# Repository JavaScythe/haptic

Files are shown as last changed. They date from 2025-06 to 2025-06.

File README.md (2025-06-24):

# haptic
8 channel 2A motor with flyback protection USB controller with 5 extra exposed GPIOs

Why? To take advantage of the low pricing of these motors, while driving them in a cost efficient but low latency and sufficiently powered manner.





### BOM
|Name |Quantity|Price Total  |Link  |
|---|---|---|---|
|RK-370|8|24.37|aliexpress.us/item/3256806031375057.html|
|PCBA|2 (minimum)|25.09|JLCPCB, see gerbers|

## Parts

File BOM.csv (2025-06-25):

Name | Quantity | Price | Total | Link
RK-370 | 8 | 24.37 | aliexpress.us/item/3256806031375057.html
PCBA | 2 | 25.09 | JLCPCB see gerbers

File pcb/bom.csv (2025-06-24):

Designator | Footprint | Quantity | Value | LCSC Part #
C1, C2 | 0603 | 2 | 10uF
C3 | 0603 | 1 | 100nF
C4 | 0603 | 1 | 1nF
D1, D3, D4, D5, D6, D7, D8, D9 | D_SOD-123 | 8 | D
D2 | 0603 | 1 | 0603
J1 | PinHeader_1x05_P2.54mm_Vertical | 1 | SWD
J2 | CONN-TH_DB301V-3.5-2P-GN | 1 | Vin
J3 | CONN-TH_DB301V-3.5-2P-GN | 1 | Common High
J4 | PinHeader_1x03_P2.54mm_Vertical | 1 | Extra
J5, J6, J7, J8 | CONN-TH_DB301V-3.5-2P-GN | 4 | Motor
Q1, Q2, Q3, Q4, Q5, Q6, Q7, Q8 | SOT-23 | 8 | AO3400A
R1, R2 | 0603 | 2 | C107701
R10, R12, R13, R14, R15, R6, R8 | 0603 | 7 | 100
R11, R16, R17, R18, R19, R7, R9 | 0603 | 7 | 10k
R20 | 0603 | 1 | 1M
R3 | 0603 | 1 | C98220
R4 | 0603 | 1 | C105588
R5 | 0603 | 1 | C22548
TP1 | TestPoint_Pad_1.0x1.0mm | 1 | TP23
TP2 | TestPoint_Pad_1.0x1.0mm | 1 | TP27
U1 | QFN-24-1EP_4x4mm_P0.5mm_EP2.6x2.6mm | 1 | ATSAMD11D14A-M
U2 | SOT-666 | 1 | USBLC6-2P6
U3 | SOT-23-5 | 1 | MIC5504-3.3YM5
USB1 | USB-MINI-SMD_U-M-M5DD-W-1 | 1 | U-M-M5DD-W-1 | C145778

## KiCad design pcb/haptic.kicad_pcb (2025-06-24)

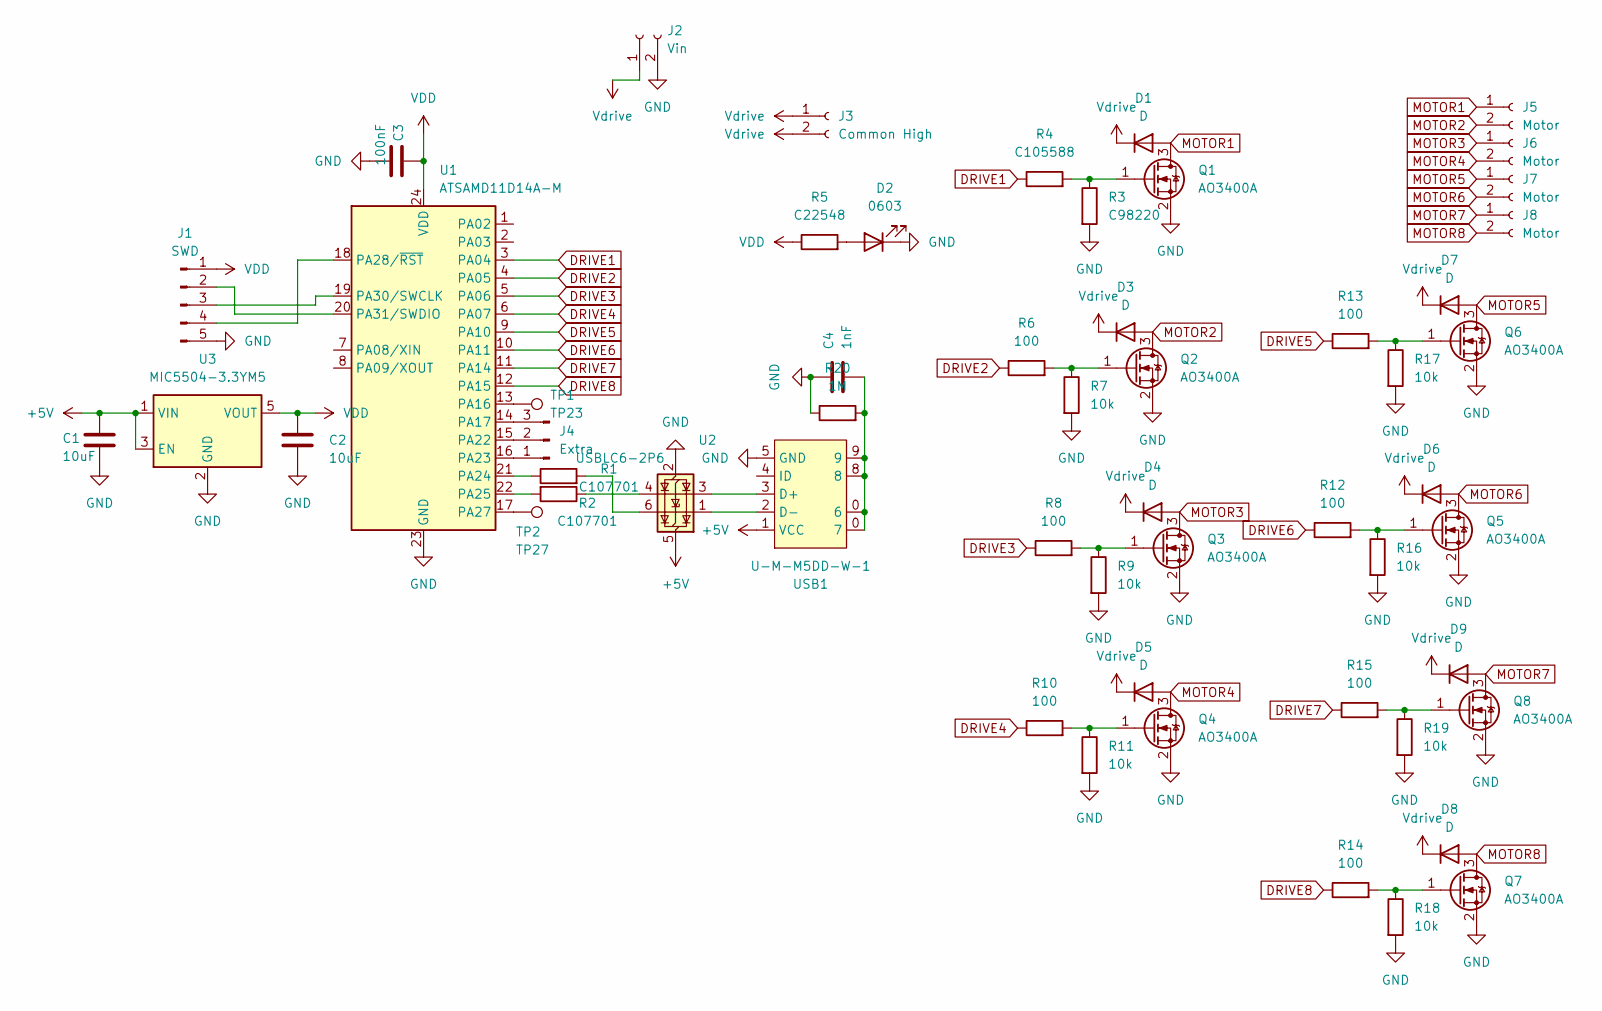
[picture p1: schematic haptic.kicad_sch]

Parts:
C1, C2: 10uF; C_0603_1608Metric
C3: 100nF; C_0603_1608Metric
C4: 1nF; C_0603_1608Metric
D1, D3, D4, D5, D6, D7, D8, D9: D; D_SOD-123
D2: 0603; LED_0603_1608Metric
J1: SWD; PinHeader_1x05_P2.54mm_Vertical
J2: Vin; CONN-TH_DB301V-3.5-2P-GN
J3: Common High; CONN-TH_DB301V-3.5-2P-GN
J4: Extra; PinHeader_1x03_P2.54mm_Vertical
J5, J6, J7, J8: Motor; CONN-TH_DB301V-3.5-2P-GN
Q1, Q2, Q3, Q4, Q5, Q6, Q7, Q8: AO3400A; SOT-23
R1, R2: C107701; R_0603_1608Metric
R3: C98220; R_0603_1608Metric
R4: C105588; R_0603_1608Metric
R5: C22548; R_0603_1608Metric
R6, R8, R10, R12, R13, R14, R15: 100; R_0603_1608Metric
R7, R9, R11, R16, R17, R18, R19: 10k; R_0603_1608Metric
R20: 1M; R_0603_1608Metric
TP1: TP23; TestPoint_Pad_1.0x1.0mm
TP2: TP27; TestPoint_Pad_1.0x1.0mm
U1: ATSAMD11D14A-M; QFN-24-1EP_4x4mm_P0.5mm_EP2.6x2.6mm
U2: USBLC6-2P6; SOT-666
U3: MIC5504-3.3YM5; SOT-23-5
USB1: U-M-M5DD-W-1; USB-MINI-SMD_U-M-M5DD-W-1; LCSC Part C145778

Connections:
+5V: C1.1, U2.5 (VBUS), U3.1 (VIN), U3.3 (EN), USB1.1 (VCC)
DRIVE1: R4.1, U1.3 (PA04)
DRIVE2: R6.1, U1.4 (PA05)
DRIVE3: R8.1, U1.5 (PA06)
DRIVE4: R10.1, U1.6 (PA07)
DRIVE5: R13.1, U1.9 (PA10)
DRIVE6: R12.1, U1.10 (PA11)
DRIVE7: R15.1, U1.11 (PA14)
DRIVE8: R14.1, U1.12 (PA15)
GND: C1.2, C2.2, C3.2, C4.1, D2.1 (K), J1.5, J2.2, Q1.2 (S), Q2.2 (S), Q3.2 (S), Q4.2 (S), Q5.2 (S), Q6.2 (S), Q7.2 (S), Q8.2 (S), R3.2, R7.2, R9.2, R11.2, R16.2, R17.2, R18.2, R19.2, R20.1, U1.23 (GND), U2.2 (GND), U3.2 (GND), USB1.5 (GND)
MOTOR1: D1.2 (A), J5.1, Q1.3 (D)
MOTOR2: D3.2 (A), J5.2, Q2.3 (D)
MOTOR3: D4.2 (A), J6.1, Q3.3 (D)
MOTOR4: D5.2 (A), J6.2, Q4.3 (D)
MOTOR5: D7.2 (A), J7.1, Q6.3 (D)
MOTOR6: D6.2 (A), J7.2, Q5.3 (D)
MOTOR7: D9.2 (A), J8.1, Q8.3 (D)
MOTOR8: D8.2 (A), J8.2, Q7.3 (D)
unnamed: D2.2 (A), R5.2
unnamed: J1.2, U1.20 (PA31/SWDIO)
unnamed: J1.3, U1.19 (PA30/SWCLK)
unnamed: J1.4, U1.18 (PA28/~RST)
unnamed: J4.1, U1.16 (PA23)
unnamed: J4.2, U1.15 (PA22)
unnamed: J4.3, U1.14 (PA17)
unnamed: Q1.1 (G), R3.1, R4.2
unnamed: Q2.1 (G), R6.2, R7.1
unnamed: Q3.1 (G), R8.2, R9.1
unnamed: Q4.1 (G), R10.2, R11.1
unnamed: Q5.1 (G), R12.2, R16.1
unnamed: Q6.1 (G), R13.2, R17.1
unnamed: Q7.1 (G), R14.2, R18.1
unnamed: Q8.1 (G), R15.2, R19.1
unnamed: R1.2, U2.6 (I/O1)
unnamed: R2.1, U2.4 (I/O2)
unnamed: TP1.1, U1.13 (PA16)
unnamed: R1.1, U1.21 (PA24)
unnamed: R2.2, U1.22 (PA25)
unnamed: TP2.1, U1.17 (PA27)
unnamed: C4.2, R20.2, USB1.0 (7), USB1.8, USB1.9
unnamed: U2.3 (I/O2), USB1.3 (D+)
unnamed: U2.1 (I/O1), USB1.2 (D-)
VDD: C2.1, C3.1, J1.1, R5.1, U1.24 (VDD), U3.5 (VOUT)
Vdrive: D1.1 (K), D3.1 (K), D4.1 (K), D5.1 (K), D6.1 (K), D7.1 (K), D8.1 (K), D9.1 (K), J2.1, J3.1, J3.2

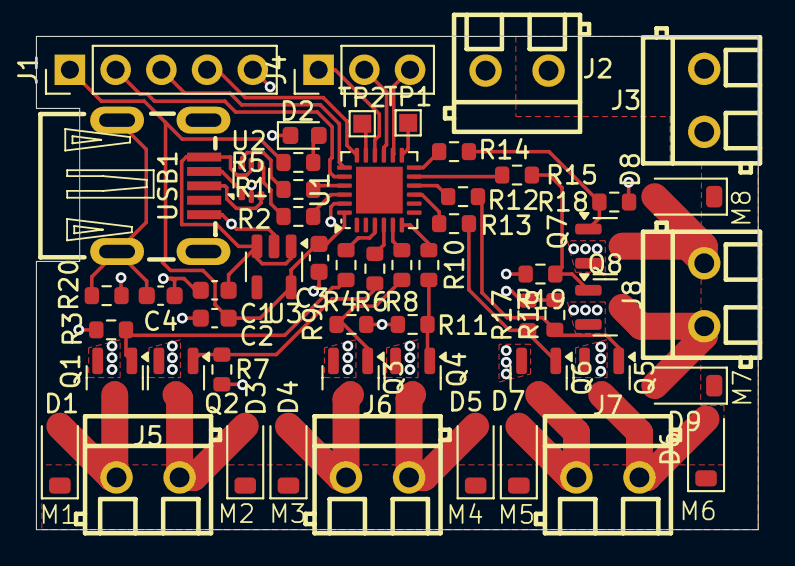
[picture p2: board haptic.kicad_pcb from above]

Board: 2 copper layers, 40.1 x 27.4 mm, 55 parts (0 on the bottom side), 44 nets.

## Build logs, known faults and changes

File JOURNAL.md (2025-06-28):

---
title: "haptic"
author: "JavaScythe"
description: "8 channel 2A motor with flyback protection USB controller with 5 extra exposed GPIOs"
created_at: "2025-6-18"
---

20 Hours total

### 06-18-25: Research and Initation
A post in the r/simracing discord led me to this link: https://www.printables.com/model/1276952-diy-simagic-p-hpr-neo-clone

The motors only 1.5$? Easy steal for something like this. Obviously I wouldn't use the commerical controller they are supposed to work with, so designing my own was the next move.

I decided on 8 channels because while overkill, it keeps the PCB small but still maximizes performance for cost.



I looked into some MCUs and FETs on JLCPCB and came up with ATSAMD11D14A and AO3400A, economical and perfect for this use case

1 Hour

### 06-19-25: Schematic Creation
Now to pick parts: USB header, screw terminals, USB protector.

Downloaded the docs for all of them and spent a flight connecting them in schematic, as well as the other components


8 Hours

### 06-21-25: PCB Creation
Routing everything on one layer to preserve the high current ground plane. Each motor is like 2A max max max so this enourmous plane is just fine for 8.



This took another flight and some addtional pre and post time.

7 Hours

### 06-22-25: Part Selection
Finding appropriate JLCPCB parts for PCBA, and uploading the Gerbers to test the prices.

I didn't account for the extended component library or whatever when choosing parts, and those are a 3$ each cost, so I need to find alternatives for those. It was about 56$ with those, and about half of that price was because of the extended.

With replacements for those, the PCB should be about 25$ and that means about 7-8 motors.



2 Hours

### 06-23-25: Swapping extended parts for basic
Changing the pieces did indeed have a great effect on the price


This means 8x motor will fit confortably in the BOM.

2 Hours
